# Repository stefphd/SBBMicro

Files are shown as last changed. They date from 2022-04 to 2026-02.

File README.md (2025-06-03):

# Introduction

This repository contains the source code for the self-balancing-bike micro-controller unit (Teensy 4.1-based 🚀️).
The introduction shows the files and folders contained in this repository and how they are organized, the prerequisites necessary, and the procedures to be used in order to build and upload the code, to generate the documentation, and to automatically generate the control-algorithm code from the Simulink model (using matlab tools).

Windows is officially supported, although compilation is also implemented for Linux. MacOS is NOT supported. 

## Files

Files:

* `controlModel.slx`: control model implementation in Simulink
* `gencode.m`: MATLAB function for code generation from Simulink model
* `params.sldd`: Simulink parameters used in `controlModel.slx`
* `build_linux.sh`: build shell script for Linux
* `build_win.bat`: build shmell script for Windows
* `Doxyfile`: configuration file for documentation generation from source code using *doxygen*
* `Makefile`: makefile for building, uploading and documentation generation using *make*
* `startup.m`: startup file for MATLAB (just to add necessary path)
* `INSTALL_PREREQ.md`: guide for the installation of the pre-requisites
* `README.md`: readme file

Code folders:

* `./include`: contains `.h` files included in source code
* `./src`: contains source `.c` or `.cpp` files, including main file `main.cpp`
* `./lib`: contains a folder for each used library, with file `library.properties` for defining the library properties (mandatory for arduino compiling) and `.h` and `.cpp` files (possibly contained in folder `./src/`)
* `./tools/teensy`: contains the core code for the Teensy microcontroller

Additional folders:

* `./tools/teensy-windows`: build tools for Windows
* `./tools/teensy-linux`: build tools for Linux
* `./docs/html`: contains the documentation in html (generated automatically from source code using *doxygen*)
* `./docs/extra`: contains extra documentation (user-written), which is included using *doxygen*
* `./matlab-tools`: contains matlab tools usefull for code generation and other stuff
* `./hardware`: contains the kicad project files
* `./.vscode`: contains VS code property file(s)
* `./.build` and `.cache`: hidden folders created only during compilation

## Pre-requisites

* *MATLAB/Simulink* with the *Embedded Coder Toolbox* installed (>=2021a), for control algorithm code generation only

No other dependecies are necessary: all used libraries are already included in `./lib/`.

Additional utilities (only recommended):

* *make* to build using the `Makefile`; alternativelly, shell or MATLAV scripts can be used
* *Visual Studio Code* with *C/C++* extension for code completation
* *Doxygen* to generate the documentation
* *KiCad* to open the schematic files in `./hardware`

See the installation guide for the pre-requisites for details.

## Documentation

Documentation for the source code and the user-defined libraries (but not for other third-party libraries) can be generated from the source using *Doxygen* with

```bash
doxygen
```

or using *make*

```bash
make doc
```

Generated documentation includes only a html version in `./docs/html`, with main file `index.html`. Documentation is also available on <https://stefphd.github.io/SBBMicro/>.
A latex documentation may be also generated by setting

```doxygen
GENERATE_LATEX  = YES
```

in `Doxyfile`. The latex version will be in `./docs/latex`, and can be compiled using latex with

```bash
cd ./docs/latex
make
```

which generates the pdf file `./doc/latex/refman.pdf`.

\attention Latex documentation requires having both *latex* and *make* installed.

## Code generation

Code generation of the control algorithm is performed via *MATLAB/Simulink* with the *Embedded Coder Toolbox*. Other toolboxes may be required. Code generation can be launch with *MATLAB* using

```MATLAB
startup;
gencode
```

The general usage of this function is

```MATLAB
startup;
gencode(modelname,dest_dir);
```

where `modelname` is the name of the Simulink model (without the `*.slx` extension included), while `dest_dir` is the destination directory: generated code is placed in `./dest_dir/modelname/src`. If no modelname is given, the function uses the first `*.slx` file found in the current directory. If no destination directory is given, the functions uses `./lib`. Code generation may be also performed using *make*, however this may take some time.

\note Toolboxes required by the code generation can be shown by running in MATLAB

```MATLAB
startup;
check_toolbox();
```

\attention For a correct usage in this project the above functions should be run in the main directory, and not in `./matlab-tools/`.

## Building

Compilation is performed using the *arduino-builder*. Bash scripts provide simple usage depending on the operative system:

* Linux:
  
  ```bash
  ./build_linux.sh
  ```
  
  or
  
  ```bash
  bash build_linux.sh
  ```
  
  \note Tested with Arch-Linux x64.

* Windows:
  
  ```bash
  ./build_win.bat
  ```
  
  \note Tested with Windows 10 x64.

* MacOS: not implemented yet, however it should be similar to Linux.

Alternatively, one can use `ctrl+shift+B` to build the code in *Visual Studio Code* with both Linux and Windows (this makes use of `build_linux.sh` or `build_win.sh` depending on the operative system). One may also use *make* the building and uploading.

\note The above shell scripts perform both the building and the uploading: it is not possible to build or upload only.

## Make tools

One may also use *make* for the building, uploading and the documentation generation. This allows several operations using similar syntax, so as to perform single operations at a time:

* `make` or `make all` to build and upload the code.
* `make build` to build the code only
* `make upload` to upload code only
* `make clean` to clean the build and cache directories
* `make remake` to clean, build and upload the code
* `make rebuild` to clean and rebuild
* `make doc` to build the documentation
* `make cleandoc` to clean the documentation
* `make help` to print the Makefile help

\note The above commands can be also used at the same time, e.g. `make build doc` to build and generate the documentation.

## MATLAB make

As an alternative to `make` and `gencode`, the code generation, buiding, uploading and documentation generation may be also performed at the same time from within the MATLAB command window. This employs a MATLAB function name `make` in `./matlab-tool/`. The function must be used inside MATLAB with the following syntax:

* `make all` or just `make` to generate code from the Simulink model, build and upload

* `make gencode` to generate the code only from the Simulink model. Note that this corresponds to call `gencode` with no input arguments, i.e. the first `*.slx` file found is used

* `make build` to build the code

* `make upload` to upload the code

* `make clean` to clean the build and cache directories

* `make remake` to clean, build and upload the code

* `make rebuild` to clean and rebuild

* `make doc` to build the documentation

* `make cleandoc` to clean the documentation

* `make help` to print the help.

\note Note that this function emulates the function `gencode` and the standard `make` commands. However, it does not require having `make` installed but only `doxygen` for the generation of the documentation.

\note The above commands can be also used at the same time, e.g. `make build doc` to build and generate the documentation.

## Known issues

* Undefined identifiers found by Visual Studio Code, however this is only a C/C++ IntelliSense issue (compilation works fine)

\todo Doc: Documentaton for Simuling and code generation???
\todo Make Arduino functions working in Simulink when compiling (maybe declare Arduino functions as external in Simulink, so as the linker links them)
\todo To implement brake motor

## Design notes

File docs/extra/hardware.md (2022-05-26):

# Hardware

The following figure shows the hardware scheme of the controller unit. The hardware is divided in two separated boxes:
* low-voltage (LV) box: contains the micro-controller unit (MCU) and the sensors
* high-voltage (HV) box: contains (mainly) the motor drivers

Hardware scheme

## Low-voltage box

The hardwares contained in the LV box are:
* Teensy 4.1 MCU, which deals with control loop execution, sensor reading, driver setting, relay enabling, and communincation with a remote controller. This also uses the internal voltage regulator to convert 5V to 3.3V.
* IMU ISM330DHCX, which measures accelerations (in mg) and angular velocities (in mdeg/s)
* Magnetometer (MAG) LIS3MDL, which measures the magnetic field in mG
* Ultimate GPS from Adafruit
* Teensy 4.0 MCU, which reads the rotary encoder for the bicycle speed measurement
* Reveiver Archer M+, which communicates with the remote controller
* Amplifier module MecoStrain 2038, which reads the full-bridge strain gauges for the rider's torque measurement
  
The base voltage level, used for digital signals, is 3.3V. In addition, two other voltage levels are present; 5V (used to power the Teensy 4.1 micro-controller) and 12V (used for the rotary encoder and the amplifier module).

## High-voltage box

The HV box contains the following hardwares:
* Steer motor driver
* Brake motor driver A4988
* 2 voltage regulator which convert the 24V (nominal) to 5V and 12V necessary for the low-voltage box
* The main relay of the system, which is controlled by the MCU and powers the 12V voltage regulator, the brake motor driver, and the steer motor driver. Note that the 5V voltage regulator is powered directly from the battery (and not from the relay)

## Connections

The following table shows the connections between the components.

\todo Describe the hardware in details: pins used and type (pull-up/pull-down), buses used

### LV schematics

Low-voltage schematic

### HV schematics

High-voltage schematic

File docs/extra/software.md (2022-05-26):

# Software

The software documentation is divided in modules, in particular:

* Entry-point function: describes the documentation for the entry-point function, i.e. main()
* Configurations: contains general configurations, mainly using the*Define* directive. This module is in turn divided in sub-modules:
  * Bus settings: configuration parameters for buses (e.g. SPI, UART, etc.)
  * Pin settings: configuration parameters for pin used
  * Constants: factors and constants
  * Macro: definition of macros used
  * User parametets: general user-defined parameters
* Variables: declaration of the variables and objects
* User functions: general user functions used in main(). These deals with sensor reading, control loop execution, driver setting, and error checking
* Data logging: functions for data logging
* MTP: functions for the MTP mode
* Debugging: functions for debugging and signal straming to and from PC

## Basic code

\todo Basic code description (i.e. the user functions)

## Data logging

By default the microcontroller logs the input and output signal of the control loop. THe log file has extension `*.sbb` and is saved in the internal SD memory, which can be read using the MTP mode. The log file is a binary file, containing a number of data chunk consisting of 64-floats, each of them having 4 bytes. For example, the data may be read from MATLAB using

```matlab
fid = fopen(logfilename); %id of the log file (extension *.sbb)
data_vector = fread(fid,'single'); %vectorized data (single, i.e. float)
N = numel(data_vector)/64; %number of samples logged
data_matrix = reshape(data_vector, [64, N])'; %reshape to have N x 64 matrix data, i.e. each column is a signal
```

## MTP mode

MTP mode allows to recognize the microcontroller as an MTP device (see e.g. [https://en.wikipedia.org/wiki/Media_Transfer_Protocol](https://en.wikipedia.org/wiki/Media_Transfer_Protocol)), in order to be capable of getting log files (with extension `*.sbb`) from the internal SD memory.
To enter in MTP mode, it is sufficient to keep the on/off button pressed for at least 3s when turning on. To get the MTP mode working in the PC side:

* Windows: no additional operation is usually necessary, the microcontroller should be automatically recognized as an MTP device
* Linux: install*gMTP* (from[https://gmtp.sourceforge.io/downloads.htmls](https://gmtp.sourceforge.io/downloads.htmls)), which is a MTP client for UNIX and UNIX like systems (this should include the*libmtp* library)

## Debugging

\todo Describe signal streaming and debugging to and from PC

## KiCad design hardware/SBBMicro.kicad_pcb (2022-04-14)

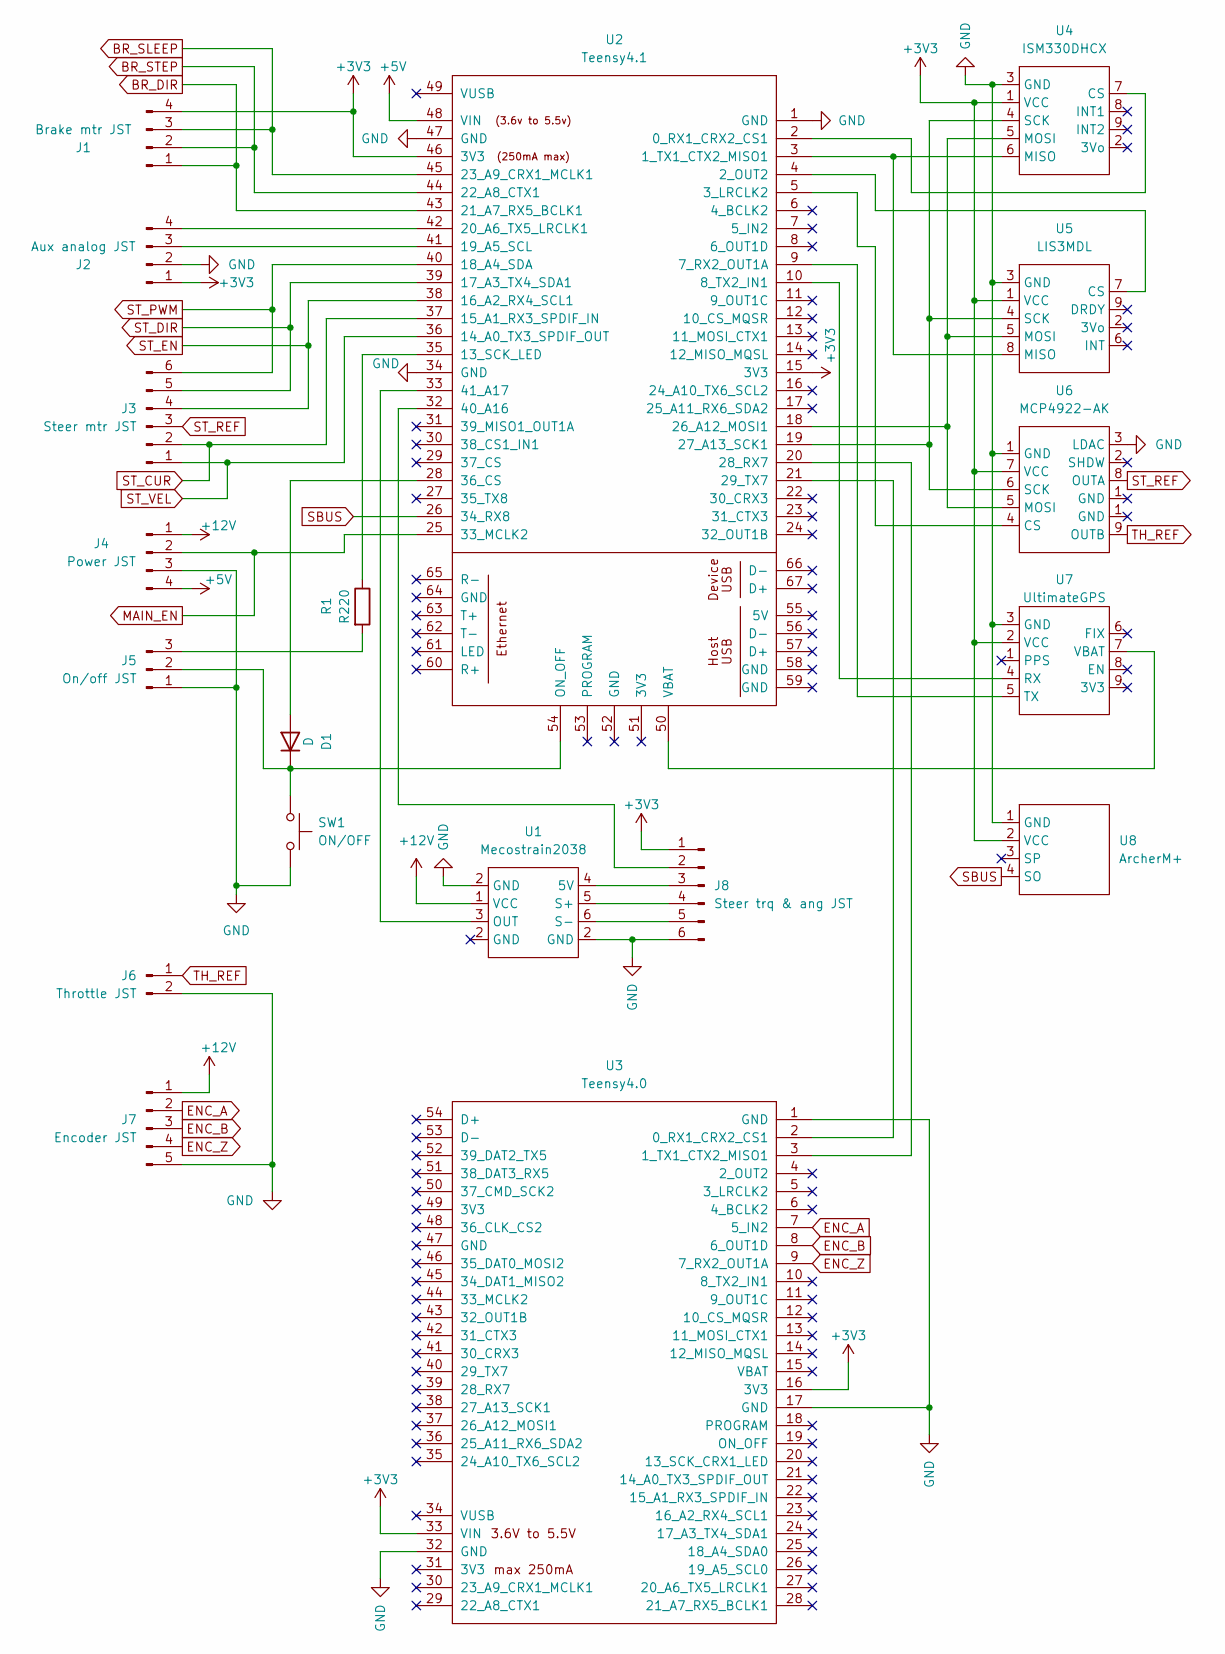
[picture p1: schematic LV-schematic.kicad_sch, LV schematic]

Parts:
D1: D; D_DO-34_SOD68_P7.62mm_Horizontal
J1: Brake mtr JST; JST_1x04_P2.54
J2: Aux analog JST; JST_1x04_P2.54
J3: Steer mtr JST; JST_1x06_P2.54
J4: Power JST; JST_1x04_P2.54
J5: On/off JST; JST_1x03_P2.54
J6: Throttle JST; JST_1x02_P2.54
J7: Encoder JST; JST_1x05_P2.54
J8: Steer trq & ang JST; JST_1x06_P2.54
R1: R220; R_Axial_DIN0204_L3.6mm_D1.6mm_P5.08mm_Horizontal
SW1: ON/OFF; SW_PUSH_6mm
U1: Mecostrain2038; Mecostrain-2038
U2: Teensy4.1; Teensy41
U3: Teensy4.0; Teensy40
U4: ISM330DHCX
U5: LIS3MDL
U6: MCP4922-AK
U7: UltimateGPS; Ultimate-GPS
U8: ArcherM+; JST_1x04_P2.54

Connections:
+3V3: J1.4, J2.1, J8.1, U2.15 (3V3), U2.46 (3V3), U3.16 (3V3), U3.33 (VIN), U4.1 (VCC), U5.1 (VCC), U6.7 (VCC), U7.2 (VCC), U8.2 (VCC)
+5V: J4.4, U2.48 (VIN)
+12V: J4.1, J7.1, U1.1 (VCC)
BR_DIR: J1.1, U2.43 (21_A7_RX5_BCLK1); also elsewhere on the board
BR_SLEEP: J1.3, U2.45 (23_A9_CRX1_MCLK1); also elsewhere on the board
BR_STEP: J1.2, U2.44 (22_A8_CTX1); also elsewhere on the board
ENC_A: J7.2, U3.7 (5_IN2)
ENC_B: J7.3, U3.8 (6_OUT1D)
ENC_Z: J7.4, U3.9 (7_RX2_OUT1A)
MAIN_EN: J4.2, U2.25 (33_MCLK2); also elsewhere on the board
unnamed: D1.1 (K), J5.2, SW1.1, U2.54 (ON_OFF)
unnamed: D1.2 (A), U2.28 (36_CS)
unnamed: J5.3, R1.2
unnamed: J8.2, U2.32 (40_A16)
unnamed: J8.3, U1.4 (5V)
unnamed: J8.4, U1.5 (S+)
unnamed: J8.5, U1.6 (S-)
unnamed: R1.1, U2.35 (13_SCK_LED)
unnamed: U1.3 (OUT), U2.33 (41_A17)
unnamed: U2.2 (0_RX1_CRX2_CS1), U4.7 (CS)
unnamed: U2.3 (1_TX1_CTX2_MISO1), U4.6 (MISO), U5.8 (MISO)
unnamed: U2.4 (2_OUT2), U5.7 (CS)
unnamed: U2.5 (3_LRCLK2), U6.4 (CS)
unnamed: U2.9 (7_RX2_OUT1A), U7.5 (TX)
unnamed: U2.10 (8_TX2_IN1), U7.4 (RX)
unnamed: U2.18 (26_A12_MOSI1), U4.5 (MOSI), U5.5 (MOSI), U6.5 (MOSI)
unnamed: U2.19 (27_A13_SCK1), U4.4 (SCK), U5.4 (SCK), U6.6 (SCK)
unnamed: U2.20 (28_RX7), U3.3 (1_TX1_CTX2_MISO1)
unnamed: U2.21 (29_TX7), U3.2 (0_RX1_CRX2_CS1)
unnamed: J2.3, U2.41 (19_A5_SCL)
unnamed: J2.4, U2.42 (20_A6_TX5_LRCLK1)
unnamed: U2.50 (VBAT), U7.7 (VBAT)
SBUS: U2.26 (34_RX8), U8.4 (SO)
ST_CUR: J3.2, U2.37 (15_A1_RX3_SPDIF_IN); also elsewhere on the board
ST_DIR: J3.5, U2.39 (17_A3_TX4_SDA1); also elsewhere on the board
ST_EN: J3.4, U2.38 (16_A2_RX4_SCL1); also elsewhere on the board
ST_PWM: J3.6, U2.40 (18_A4_SDA); also elsewhere on the board
ST_REF: J3.3, U6.8 (OUTA); also elsewhere on the board
ST_VEL: J3.1, U2.36 (14_A0_TX3_SPDIF_OUT); also elsewhere on the board
TH_REF: J6.1, U6.9 (OUTB)

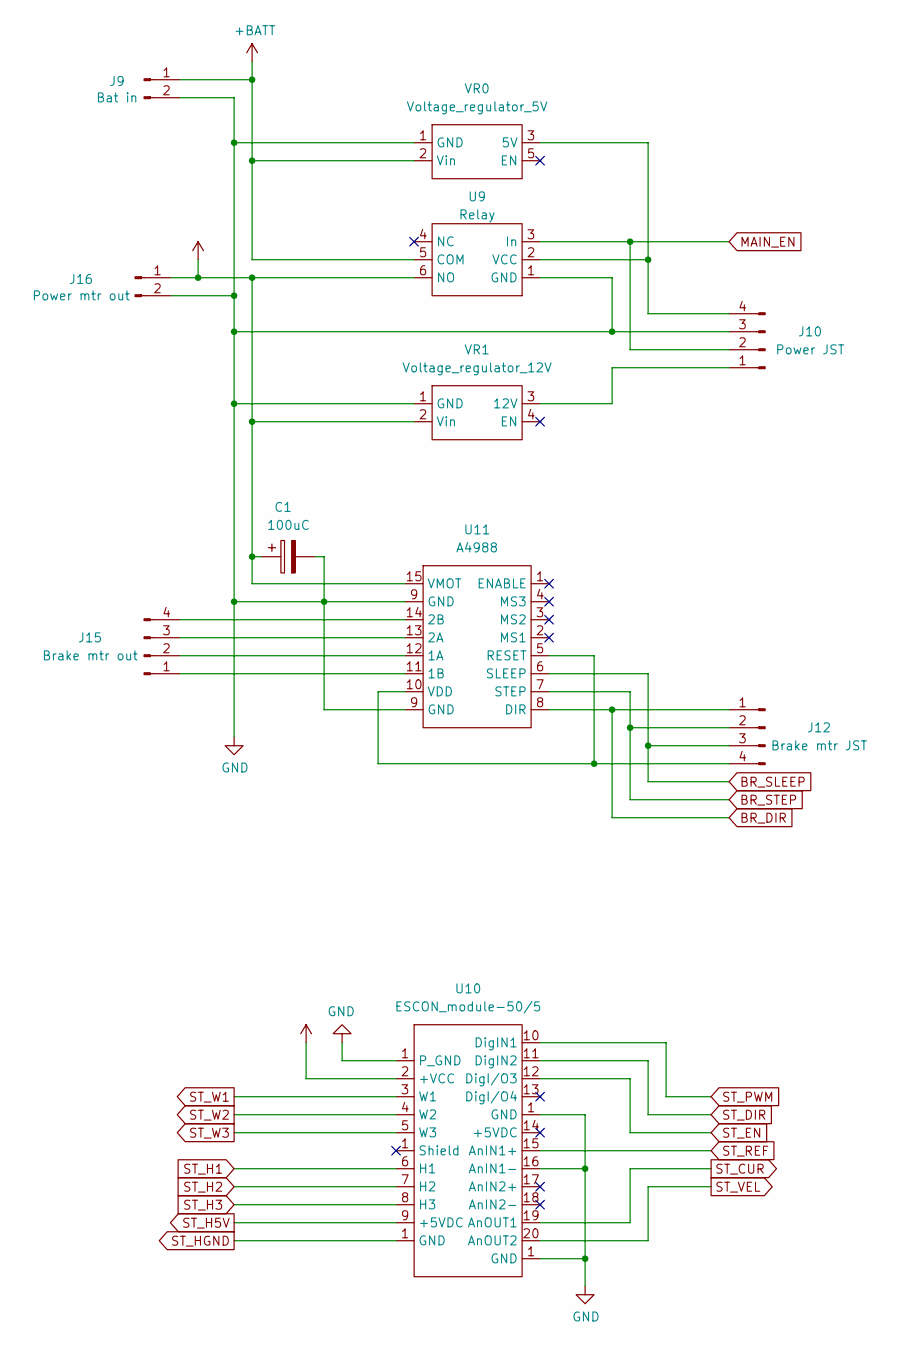
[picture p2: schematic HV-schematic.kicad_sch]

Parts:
C1: 100uC; CP_Radial_D5.0mm_P2.50mm
J9: Bat in; TerminalBlock_bornier-2_P5.08mm
J10: Power JST; JST_1x04_P2.54
J12: Brake mtr JST; JST_1x04_P2.54
J15: Brake mtr out; JST_1x04_P2.54
J16: Power mtr out; TerminalBlock_bornier-2_P5.08mm
U9: Relay
U10: ESCON_module-50/5; Escon module-50-5
U11: A4988
VR0: Voltage_regulator_5V; Voltage-reg_5V
VR1: Voltage_regulator_12V; Voltage-reg_12V

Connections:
+24V: C1.1, J16.1, U9.6 (NO), U10.2 (+VCC), U11.15 (VMOT), VR1.2 (Vin)
+BATT: J9.1, U9.5 (COM), VR0.2 (Vin)
BR_DIR: J12.1, U11.8 (DIR); also elsewhere on the board
BR_SLEEP: J12.3, U11.6 (SLEEP); also elsewhere on the board
BR_STEP: J12.2, U11.7 (STEP); also elsewhere on the board
MAIN_EN: J10.2, U9.3 (In); also elsewhere on the board
unnamed: J10.1, VR1.3 (12V)
unnamed: J10.4, U9.2 (VCC), VR0.3 (5V)
unnamed: J12.4, U11.5 (RESET), U11.10 (VDD)
unnamed: J15.1, U11.11 (1B)
unnamed: J15.2, U11.12 (1A)
unnamed: J15.3, U11.13 (2A)
unnamed: J15.4, U11.14 (2B)
ST_CUR: U10.19 (AnOUT1); also elsewhere on the board
ST_DIR: U10.11 (DigIN2); also elsewhere on the board
ST_EN: U10.12 (DigI/O3); also elsewhere on the board
ST_H1: U10.6 (H1)
ST_H2: U10.7 (H2)
ST_H3: U10.8 (H3)
ST_H5V: U10.9 (+5VDC)
ST_PWM: U10.10 (DigIN1); also elsewhere on the board
ST_REF: U10.15 (AnIN1+); also elsewhere on the board
ST_VEL: U10.20 (AnOUT2); also elsewhere on the board
ST_W1: U10.3 (W1)
ST_W2: U10.4 (W2)
ST_W3: U10.5 (W3)

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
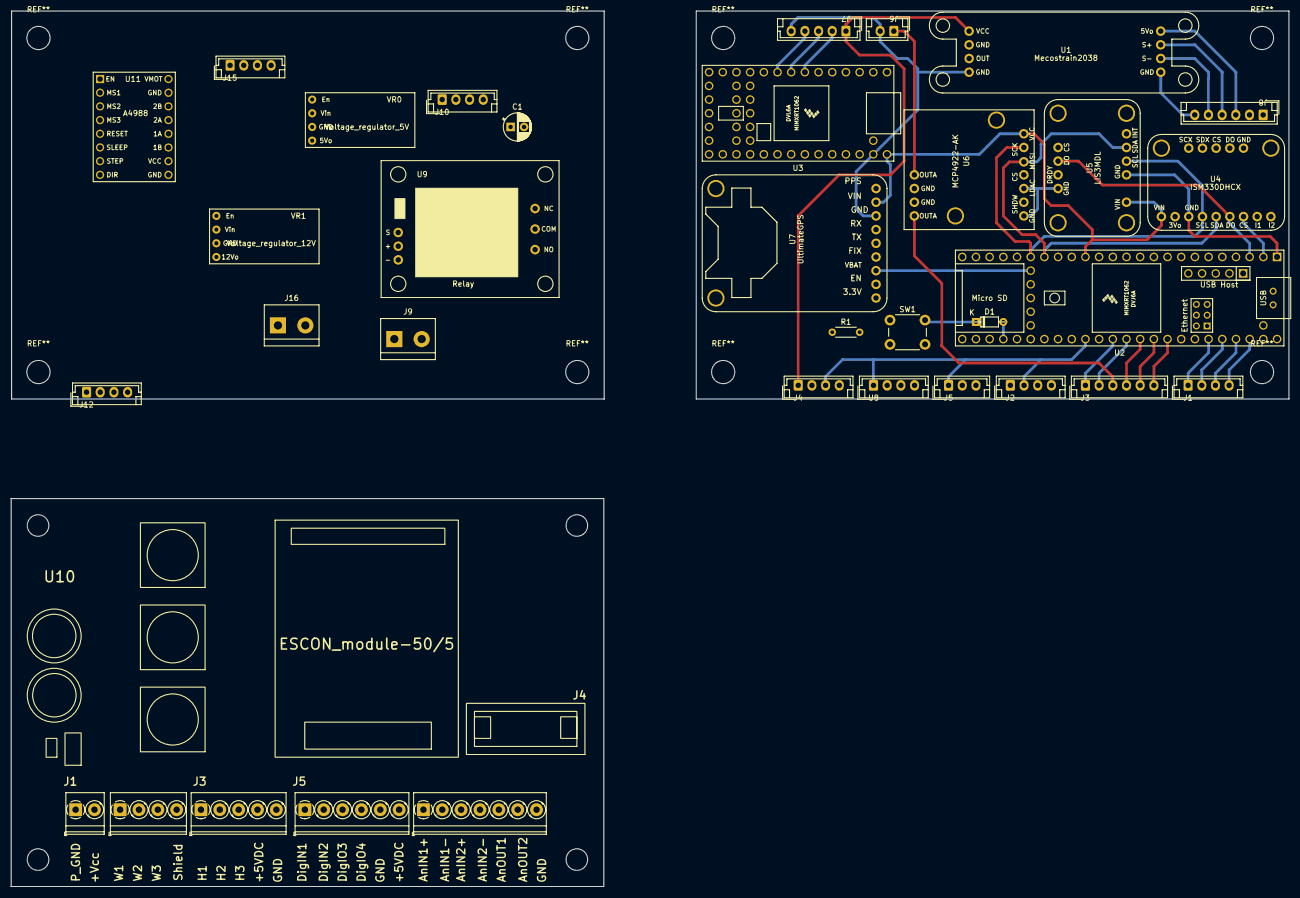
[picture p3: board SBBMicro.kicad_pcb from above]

Board: 2 copper layers, 237.2 x 162.5 mm, 30 parts (0 on the bottom side), 50 nets.

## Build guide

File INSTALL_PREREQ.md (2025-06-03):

# Installation of the pre-requisites

## Windows

### Arduino builder

Arduino builder is shipped with this repository. No installation should be necessary, although you may use your own version of arduino builder.

### Visual Studio Code

To install *Visual Studio Code*:

1. Download the installer from [here](https://code.visualstudio.com/)
2. Run the installer `VSCodeUserSetup-x64-X.X.X.exe` (where `X.X.X` is the software version)
3. Follow the installation steps

You may also install the `C/C++` extension for *Visual Studio Code* for code completation.

### Make and Doxygen

For installation of *Make* and *Doxygen* you may employ *Chocolatey*, which is a package manager for Windows. First download and install *Chocolatey* by following the this [installation guide](https://chocolatey.org/install#individual). Basically, you need to run in the powershell (with administrative privileges) the following command

```powershell
Set-ExecutionPolicy Bypass -Scope Process -Force; [System.Net.ServicePointManager]::SecurityProtocol = [System.Net.ServicePointManager]::SecurityProtocol -bor 3072; iex ((New-Object System.Net.WebClient).DownloadString('https://community.chocolatey.org/install.ps1'))
```

To install *Make* and *Doxygen* just run in the command promp or powershell (with administrative privileges)

```powershell
choco install make doxygen.install
```

and follow the installation steps (basically, type `Y` when required).
Finally, add the installation directory (default is `C:\Program Files\doxygen\bin`) to the environment variable `PATH`.
To check the installation, just use in the command prompt (you need to open a new terminal)

```bash
doxygen -v
```

```bash
make -v
```

\note Alternatively, for *Doxigen* you may also download the installer from [here](https://www.doxygen.nl/download.html) and install the software. After, you need to add the installation directory to the environment variable `PATH`.

\note For *make* other installation process may exist.

### KiCAD

Download and install *KiCAD* from [here](https://www.kicad.org/download/windows/).

## Linux

Depending on your Linux distrubution, you can easily install the pre-requisites using your package manager: **you are using Linux, so you are supposed to know this stuff!** 

## MacOS

Not implemented yet.

## Embedded Coder Toolbox (MATLAB)

For installing the *Embedded Coder Toolbox* in MATLAB
0. Install MATLAB (if not installed)
1. Go to `Add-Ons > Get Add Ons` and look for the *Embedded Coder*
2. Click on *Embedded Coder* and install

Other (possibly necessary) MATLAB toolboxes may be installed in a simular way.

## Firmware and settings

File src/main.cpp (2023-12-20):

/*! \file main.cpp
	\brief Main file of the low-level code for the controller.
	\details Main file of the low-level code for the controller. This contains the definition for main function, which is the
	entry-point function of the code. Note that this is different from the standard Arduino workflow, which makes use of the setup() and
	loop() function with the main() written in the core code (actually, the main function defined in this file overrides that
	in the core code).
	\see mainfun
*/

//include
#include <include.h>

#undef main //remove Arduino main function - maybe not necessary (?)

/*! @defgroup mainfun Entry-point function
	\brief Entry-point function of the code.
	\details This contains the definition for main function, which is the
	entry-point function of the code. Note that this is different from the standard Arduino workflow, which makes use of the setup() and
	loop() function with the main() written in the core code (actually, the main function defined in this file overrides that
	in the core code).
    \see main.cpp
    @{
*/

/*! \brief Entry-point function.
	\details Definition for main function, which is the entry-point function of the code.
	The function implementation is structured as follows

	```
	int main() {

		//initializations here

		while(1) { //infinite loop, running forever
			//loop here
		}

		return 0;
	}
	```

	\return The exit status (0 in this case).
    \see main.cpp
*/
int main() {

	//set the pins
	set_GPIO();

	//led on
	LEDON;

	//set CPU freq
	set_arm_clock(CPU_FREQ);

	//set RTC provider
	setSyncProvider(getTime);

	//set callback when swiching off
	delay(200);
	set_arm_power_button_callback(&turnoff_callback);

    //check mtp - after set_arm_power_button_callback, before enabling other relay etc
    if (check_mtp()) do_mtp(); //if true 

	//begin IO buses
	start_IObus();

	//set input-output (sensors etc)
	set_IObus();

	//start 
	start_brake_stepper();
	
	//enable relay
	RELAY_ENABLE;

	//check battery voltage
	//check_voltage();

	//do zero of sensors
	do_zeros();

	//debug if necessary (otherwise do nothing)
	start_debug();

	//start_logger if necessary (otherwise do nothing)
	start_logger();

	//enable steer motor
	MTR_ENABLE;

	//main delay before starting
	delay(200);

	//led off
	LEDOFF;

	//set custom control params
	set_ctrl_param();

	//begin control loop - to be called just before starting loop
	ctrl.begin();	

	sampling_timer = micros() - SAMPLING_TIME; //to be sure that the control loop starts immediately at the first loop

	//flush serials
	serial_flush();

	while(true) {
		if ((micros() - sampling_timer) >= SAMPLING_TIME) {
			timing.dt_cycle = micros() - sampling_timer; //cycle time (should be equal to SAMPLING_TIME)
			sampling_timer = micros(); //update timer
			
			//get sensor readings
			get_sensors();
			
			//set ctrl input-output
			set_ctrl_input();
			
			//do control loop
			do_control();

			//check if errors 
			check_error();

			//set drivers
			set_driver();

			//update duty cycle
			update_tet(sampling_timer);			

			//other secondary stuff below

			//do debug stuff if necessary (otherwise do nothing)
			do_debug();

			//do logging stuff if necessary (otherwise do nothing)
			do_logger();
			
			//do led stuff
			do_led();

	}

	//yield(); //maybe not necessary

	}

	return 0;

}

/*! @} */

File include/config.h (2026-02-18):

/*! \file config.h
	\brief General configurations for the source code.
	\details Configuration file with defines and macros for the source code of the 
	SBB Micro code. This includes PIN definitions, BUS settings, DAC settings, 
	definitions of constants and factors, conversions of raw data, 
	and other user-defined parameters.
	\note Building is necessary for changes to take effect.
	\see config bus pin constants macros userparams
*/

#ifndef __CONFIG_H__
#define __CONFIG_H__


/*! @defgroup config Configurations
	\brief Settings, defines and macros.
	\details Defines and macros for the source code of the SBB Micro code. 
	This includes PIN definitions, BUS settings, DAC settings, 
	definitions of constants and factors, conversions of raw data, 
	and other user-defined parameters.
	\note Building is necessary for changes to take effect.
   @{
*/
//....................................BUSES....................................

/*! @defgroup bus Bus settings
   \brief Settings for the buses.
   \details Settings of the used buses for the communications with sensorsaand drivers. 
   This includes defines for the SPI and UART(s) used for the sensors, settings for the
   ADCs, DACs, and PWM.
	\warning Be careful to modify this parameters. Changes may lead to possible short circuits which kill the circuit.
   @{
 */

//SPI
#define USED_SPI		SPI1 //!< Used SPI for sensor IO bus.
#define SPISPEED_IMU	10e6 //!< Speed of IMU SPI, max is 10e6.
#define SPISPEED_MAG	10e6 //!< Speed of MAG SPI, max is 10e6.
#define SPISPEED_DAC	10e6 //!< Speed of MAG SPI, max is 20e6.

//UART
#define UART_SPEEDSENS	Serial7 //!< Used UART for speed sensor bus.
#define BAUD_SPEEDSENS	4e6 //!< Baudrate of the UART for speed sensor bus.
#define UART_GPS		Serial2 //!< Used UART for GPS sensor bus.
#define BAUD_GPS_DEF	9600 //!< Default baudrate of GPS sensor (for init only).
#define BAUD_GPS		57600 //!< Actual baudrate of GPS sensor.
#define GPS_EXTBUFSIZE	128 //!< Extra buffer size for GPS sensor UART.
#define UART_SBUS		Serial8 //!< Used UART for SBUS communication. /details The UART used for the SBUS receiver. This runs with a baudrate of 100000. Initialization and setting is performed by the SBUS library.

//ADC
#define ADC_RES			12 //!< ADC resolution (in bits).
#define ADC_AVERAGE		8 //!< ADC averaging 1/2/8/16 (samples). The more the averaging, the less the noise, but the more the reading time.

//DAC
#define DAC_RES			12 //!< DAC resolution (in bits).
#define DAC_MTR_CH		0 //!< DAC channel for motor control.
#define DAC_THROTTLE_CH 1 //!< DAC channel for throttle control.

//PWM
#define PWM_RES			12 //!< PWM resolution in bit (max is 14).
#define PWM_FREQ		5e3 //!< PWM frequency (max is 5kHz).
#define PWM_MIN			0.1F //!< Minimum PWM value for motor current reference.
#define PWM_MAX			0.9F //!< Maximum PWM value for motor current reference.

/*! @} */ 

//.....................................PINS....................................

/*! @defgroup pin Pin settings
   \brief Settings for the pins.
   \details Used pins in the Teensy 4.1 microcontroller. 
   This includes the chip-select pins used for the SPI, analog input
   pin to read analog signals, PWM pin, and digital in and out pins.
   \warning Be careful to change the pin settings. Changes may lead to possible short circuits which kill the circuit.
   @{
 */

//SPI CS PINS
#define CS_IMU			0 //!< Chip select pin of IMU.
#define CS_MAG			2 //!< Chip select pin of MAG.
#define CS_DAC			3 //!< Chip select pin of DAC.

//ANALOG PINS
#define STEER_POS		A16 //!< Steer position analog input pin.
#define STEER_SPEED		A0 //!< Steer speed analog input pin.
#define ACT_CURR		A1 //!< Actual current analog input pin.
#define RIDER_TRQ		A17 //!< Rider torque analog input pin.
#define VOLTAGE			A15 //!< Battery voltage analog input pin.
#define FORK_DISP		A14 //!< Front fork displacement analog input pin.

//PWM
#define PWM_PIN			18 //!< PWM pin for motor current reference.

//DIGITAL OUT
#define MTR_EN_PIN		16 //!< Digital out for motor enable.
#define MTR_DIR_PIN		17 //!< Digital out for motor direction.
#define RELAY_EN_PIN	33 //!< Digital out for relay enable.
#define BR_DIR_PIN		21 //!< Digital out for brake motor direction.
#define BR_STEP_PIN		22 //!< Digital out for brake motor step.
#define BR_SLEEP_PIN	23 //!< Digital out for brake motor sleep.

//DIGITAL IN 
#define ONOFF_STATE_PIN	36 //!< Digital in for on/off buttun state (diode between onoff and this).

/*! @} */ 

//.............................CONSTANTS & FACTORS.............................

/*! @defgroup constants Constants
   \brief Constant and factor definitions.
   \details Definition of the constants and factors. 
   This includes the fundamental sampling time and the sampling factors for sensors etc. 
   (expressed in units of the fundamental sempling time), the output data rate of sensors, 
   the gains, offsets, and conversions for sensors and units, and limits values.
   @{
 */
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

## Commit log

2022-02-21 Add teensy core and hardware
2022-02-21 Add do_led()
    do_led() function for status LED added
2022-02-22 Remove hardware/tools
    hardware/tools replaced will be replaced by hardware/tools-windows and hardware/tools-linux depending on the OS
    [config.h]
2022-02-22 Add teensy_loader_cli.exe
    Binaries of Tensy loader for Windows x64 added (compiled using MSYS2)
2022-02-22 Update build_win.bat
    Uploading hex file using teensy_loader_cli added
2022-02-22 Create prototypes.h
    Create prototypes.h to declare all functions before their implementation
2022-03-18 Revert "Remove darkmode in docs"
    This reverts commit d5472c3890c3957315ce68cd81f913eb3c3c7be8.
    [config.h, objects.h]
2022-03-18 Remove teensy3 from core
    teeensy3 is not used, remove it
2022-03-18 Remove loop() and setup()
    User-defined main() used instead of loop() and setup() (employed in Arduino workflow)
2022-04-13 Update lv schematics
2022-04-13 Add kicad project
    [HV-schematic.kicad_sch, LV-schematic.kicad_sch, SBBMicro.kicad_pcb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]
2022-04-13 Update kicad
    [HV-schematic.kicad_sch, LV-schematic.kicad_sch]
2022-04-14 Update kicad and doc
    [HV-schematic.kicad_sch, LV-schematic.kicad_sch, SBBMicro.kicad_sch]
2022-04-20 Change directories
    ./hardware renamed to ./build-tools
    ./kicad renamed to ./hardware
    [HV-schematic.kicad_sch, LV-schematic.kicad_sch, SBBMicro.kicad_pcb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]
2022-04-20 Add stepper library to ./lib
2022-04-20 Include teensystep4.h
2022-04-20 Fix bug
    Renamed arduino.h to Arduino.h to make compilation working
2022-04-20 Change directory names
    build-tools changed to tools to make window compilation working
    hardware changed to schematics
    [HV-schematic.kicad_sch, LV-schematic.kicad_sch, SBBMicro.kicad_pcb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]
2022-04-20 Revert "Change directory names"
    This reverts commit 86ba7ea09b87f8394fafa56df22d78b73fbb4c30.
    [HV-schematic.kicad_sch, LV-schematic.kicad_sch, SBBMicro.kicad_pcb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]
2022-04-20 Add brake motor
2022-04-28 Fix brake motor issues
    [config.h, debug.h, userfun.h]
2022-09-13 Fix bug: missing set_ctrl_input() in main
    [main.cpp]
2022-09-13 Update schematics
    [HV-schematic.kicad_sch, LV-schematic.kicad_sch, SBBMicro.kicad_sch]
2025-07-14 Add SE and SC switch to simulink inputs
2025-07-17 Add throttle test
2025-09-20 Change LED blinking
